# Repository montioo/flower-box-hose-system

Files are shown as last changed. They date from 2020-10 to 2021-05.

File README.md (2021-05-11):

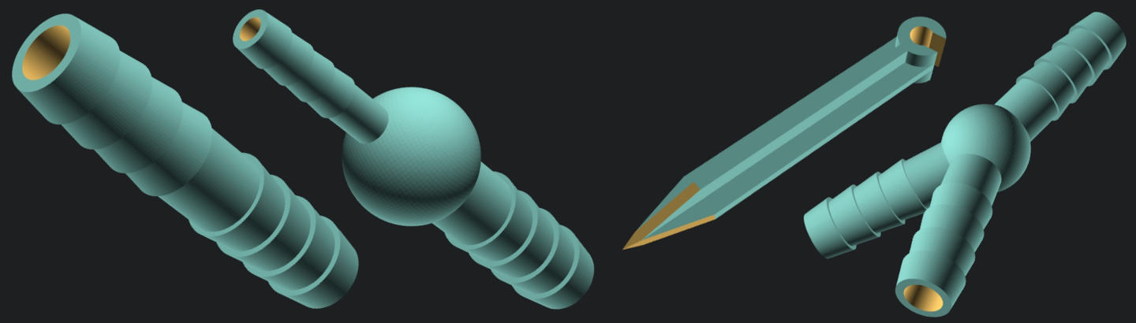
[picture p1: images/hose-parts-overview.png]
Overview Image


# flower-box-hose-system

A set of 3D printable sprinklers and hose connectors to build an automatic watering system for flower boxes, e.g. on your balcony.

This project is licensed under the terms of the GNU General Public License v3.0.

Author: Marius Montebaur

## Print Settings

Detailed descriptions on how to adjust the print settings can be found [here](https://montebaur.tech/projects/waterproof_3d-printing.html).

Summary: To make the components waterproof adjustments to the print setting are necessary (parameter names from Cura)
- Infill density: `100%`
- Wall thickness: 4 lines
- Flow (or extrusion multiplier): `108%`. Tells the printer to use more filament than necessary to close gaps between neighboring filament lines.
  - If your slicer is capable of setting different values for the flow used for the object and the support material, stick with 100% flow for the support material. Otherwise, removing the support will be more difficult.
- Printing Temperature: `215°C`. A bit hotter than usual to make the filament flow better.
- Try to orient the objects on the print bet such that the water flow direction is along the z axis ([explanation](https://montebaur.tech/projects/waterproof_3d-printing.html#object-orientation)).

## Changelog

### 2021-05-11:
- Added hose end cap.
- New wall connector that allows mounting a hose extender on a wall, e.g. of a plastic enclosure containing magnetic valves.

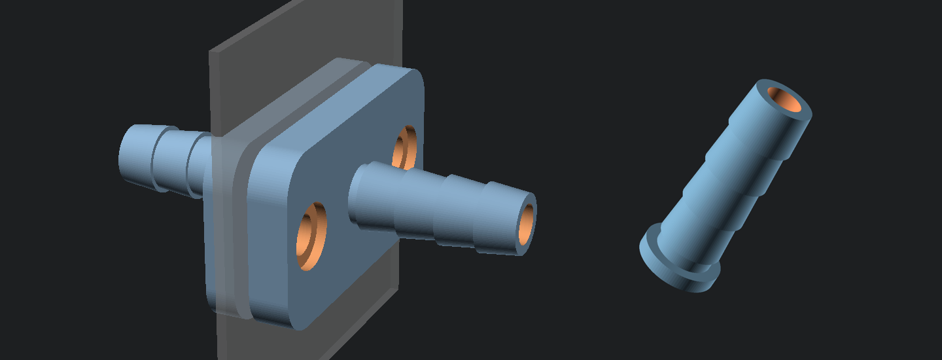
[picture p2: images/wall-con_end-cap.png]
New wall connector


### 2021-05-09:
- Added parameters for hoses with 6mm inner diameter (`Parameters.scad`)
- Updated box shaped splitter (`HoseSplitter_BoxShape.scad`) to accept different inlet and outlet diameters and added numbers on the housing.

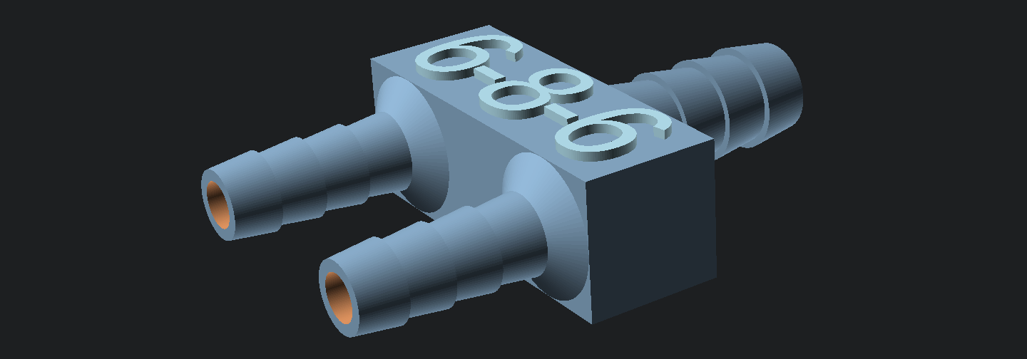
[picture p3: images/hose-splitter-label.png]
New box shaped connectors with labels for inner hose diameters.


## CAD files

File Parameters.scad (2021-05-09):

//
//  Parameters.scad
//  flower-box-hose-system
//
//  Author: Marius Montebaur
//  montebaur.tech, github.com/montioo
//

//
// Parameterization for Hose Connectors.
//
// This file holds the measures that are employed by all adapters.
// Additional information is available here:
//  https://montebaur.tech/hose_connectors.html


// Parameters for 8mm x 1.5mm hoses
// (8mm inner diameter and the wall strength: 8mm + 2*1.5mm = 11mm diameter)
// ===============================================

// inner and outer diameter refer to the 3D printed connectors, NOT the hose.
hc8mm_pipe_inner_dia = 5.4;
hc8mm_pipe_outer_dia = 8;
hc8mm_outer_dia_lower = 7.75;
hc8mm_outer_dia_upper = 9;
hc8mm_tooth_length = 4.3;
hc8mm_tooth_number = 4;


// Parameters for 6mm x 1mm
// ===============================================

// inner and outer diameter refer to the 3D printed connectors, NOT the hose.
hc6mm_pipe_inner_dia = 4;
hc6mm_pipe_outer_dia = 6;
hc6mm_outer_dia_lower = 6;
hc6mm_outer_dia_upper = 6.9;
hc6mm_tooth_length = 4;
hc6mm_tooth_number = 4;


// Parameters for 4mm x 1mm
// ===============================================

// inner and outer diameter refer to the 3D printed connectors, NOT the hose.
hc4mm_pipe_inner_dia = 2.4;
hc4mm_pipe_outer_dia = 4;
hc4mm_outer_dia_lower = 4;
hc4mm_outer_dia_upper = 4.5;
hc4mm_tooth_length = 3;
hc4mm_tooth_number = 4;


// Your custom parameters ...
// 1. Add your parameterization instead of dots (...)
// 2. Add the variables to the lists below
// 3. Index your parameters by index 2 in each list (the lists
//    are imported in file in this project).
// A schematic for the parameters can be found here:
//   https://montebaur.tech/projects/hose_connectors.html#parameterization
// ===============================================

// hcXmm_pipe_inner_dia = ...;
// hcXmm_pipe_outer_dia = ...;
// hcXmm_outer_dia_lower = ...;
// hcXmm_outer_dia_upper = ...;
// hcXmm_tooth_length = ...;
// hcXmm_tooth_number = ...;


// These variables are available throughout the project (after using
// `include <Parameters.scad>`) and hold parameterizations for hoses
// with different diameters.
// A schematic for the parameters can be found here:
//   https://montebaur.tech/projects/hose_connectors.html#parameterization
hc_pipe_inner_dia =  [hc4mm_pipe_inner_dia,  hc6mm_pipe_inner_dia,  hc8mm_pipe_inner_dia  ];  // a
hc_pipe_outer_dia =  [hc4mm_pipe_outer_dia,  hc6mm_pipe_outer_dia,  hc8mm_pipe_outer_dia  ];  // b
hc_outer_dia_lower = [hc4mm_outer_dia_lower, hc6mm_outer_dia_lower, hc8mm_outer_dia_lower ];  // c
hc_outer_dia_upper = [hc4mm_outer_dia_upper, hc6mm_outer_dia_upper, hc8mm_outer_dia_upper ];  // d
hc_tooth_length =    [hc4mm_tooth_length,    hc6mm_tooth_length,    hc8mm_tooth_length    ];  // e
hc_tooth_number =    [hc4mm_tooth_number,    hc6mm_tooth_number,    hc8mm_tooth_number    ];  // #teeth

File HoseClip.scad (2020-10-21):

//
//  HoseClip.scad
//  flower-box-hose-system
//
//  Author: Marius Montebaur
//  montebaur.tech, github.com/montioo
//

$fn = 100;


// A tip or spike to stick into soil. Coordinate origin is the top part.
// @param overhang: How far the spike should extend over the coordinate origin.
// @param stick_dia: Diameter of the stick.
module Spike(overhang=20, stick_dia=12) {
    bar_thickness = 2.5;
    spire_length = 20;
    stick_length = 80;

    difference() {
        for (i = [0, 1]) {
            rotate([i*90, 0, 0]) translate([-overhang, -bar_thickness/2, -stick_dia/2])
                cube([stick_length+overhang, bar_thickness, stick_dia]);
        }

        t = 1;  // parameter for polygon generation
        for (i = [0 : 3]) {
            rotate([i*90, 0, 0]) translate([stick_length, 0, stick_dia/2])
                rotate([90, 180, 0]) translate([0, 0, -bar_thickness/2 - 0.01])
                linear_extrude(height=bar_thickness+0.02)
                polygon([[-t, -t], [-t, stick_dia/2], [0, stick_dia/2], [spire_length, 0], [spire_length, -t]]);
        }
    }
}

// Models a hose clip
// @param head_width: Width of the upper part that clips to the hose.
// @param inner_diameter: inner diameters of the clip. Should be a bit less than the hose's diameter.
module HoseClip(head_width, inner_diameter) {
    outer_diameter = max(12, inner_diameter + 2*3);
    holder_opening = inner_diameter * 0.8;

    difference() {
        union() {
            Spike(overhang=outer_diameter/2, stick_dia=head_width);
            translate([-outer_diameter/2, head_width/2, 0]) rotate([90, 0, 0]) cylinder(h=head_width, d=outer_diameter);
        }

        translate([-outer_diameter/2, head_width/2, 0]) rotate([90, 0, 0]) {
            translate([0, 0, -1]) cylinder(h=head_width + 2, d=inner_diameter);

            rotate([0, 0, 20]) translate([-holder_opening/2, 0, -1]) cube([holder_opening, outer_diameter, head_width + 2]);
        }
    }
}

// Parameterization for a 8mm x 1.5mm hose => 11mm diameter
module HoseClip8mm() {
    head_width = 12;
    inner_diameter = 10.8;  // hose has an outer diameter of 11mm
    
    HoseClip(head_width=head_width, inner_diameter=inner_diameter);
}

// Parameterization for a 4mm x 1mm hose => 6mm diameter
module HoseClip4mm() {
    head_width = 12;
    inner_diameter = 5.8;
    
    HoseClip(head_width=head_width, inner_diameter=inner_diameter);
}

// Custom clip
// module HoseClipXmm(hose_type=0) {
//     Add the diameter of your hose here:
//     hose_outer_diameter = ...;
//     head_width = 12;
//     inner_diameter = hose_outer_diameter - 0.2;
//     
//     HoseClip(head_width=head_width, inner_diameter=inner_diameter);
// }


HoseClip4mm();

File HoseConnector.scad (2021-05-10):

//
//  HoseConnector.scad
//  flower-box-hose-system
//
//  Author: Marius Montebaur
//  montebaur.tech, github.com/montioo
//

include <Parameters.scad>

$fn = 100;


// Model of the connector that fits into a tube.
// @param hose_type: Defines the type of hose this connector should fit into.
//   A list of hose indices along with a detailed explanation is given in Parameters.scad
//   Default is hose_type with id 0 (hoses with 4mm inner diameter).
module HoseConnector(hose_type=0) {
    difference() {
        for (i = [0 : hc_tooth_number[hose_type]-1]) {
            translate([0, 0, i*hc_tooth_length[hose_type]]) cylinder(
                h=hc_tooth_length[hose_type],
                d1=hc_outer_dia_upper[hose_type],
                d2=hc_outer_dia_lower[hose_type]
            );
        }
        translate([0, 0, -0.01]) cylinder(
            h=hc_tooth_number[hose_type] * hc_tooth_length[hose_type] + 2 * 0.01,
            d=hc_pipe_inner_dia[hose_type]
        );
    }
}

// Example for a connector modeled after hose_type 0:
HoseConnector(0);

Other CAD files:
HoseEndCap.scad
HoseExtender.scad
HoseSplitter_BoxShape.scad
HoseSplitter_Y-Shape.scad
HoseWallConnector.scad
SprinklerBar.scad
SprinklerRing.scad

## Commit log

2020-10-21 Repo init
    [HoseClip.scad, HoseConnector.scad, HoseExtender.scad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]
2020-10-21 Fixed typo in Adapter module and updated comments
    [HoseClip.scad, HoseConnector.scad, HoseExtender.scad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]
2020-10-22 Added comment for clarification
    [SprinklerRing.scad]
2020-10-22 Adding new sprinkler type: Bar
    [SprinklerBar.scad]
2020-10-22 fixed wrong naming
    [SprinklerBar.scad]
2021-05-09 New labels on box shaped splitter
    [HoseSplitter_BoxShape.scad, Parameters.scad]
2021-05-09 Improved water flow in Y-shaped splitter
    [HoseSplitter_Y-Shape.scad]
2021-05-09 Updated hose splitter note
    [HoseSplitter_BoxShape.scad]
2021-05-10 added new wall connector
    [HoseConnector.scad, HoseWallConnector.scad, SprinklerRing.scad]
2021-05-11 Added hose end cap
    [HoseEndCap.scad]
